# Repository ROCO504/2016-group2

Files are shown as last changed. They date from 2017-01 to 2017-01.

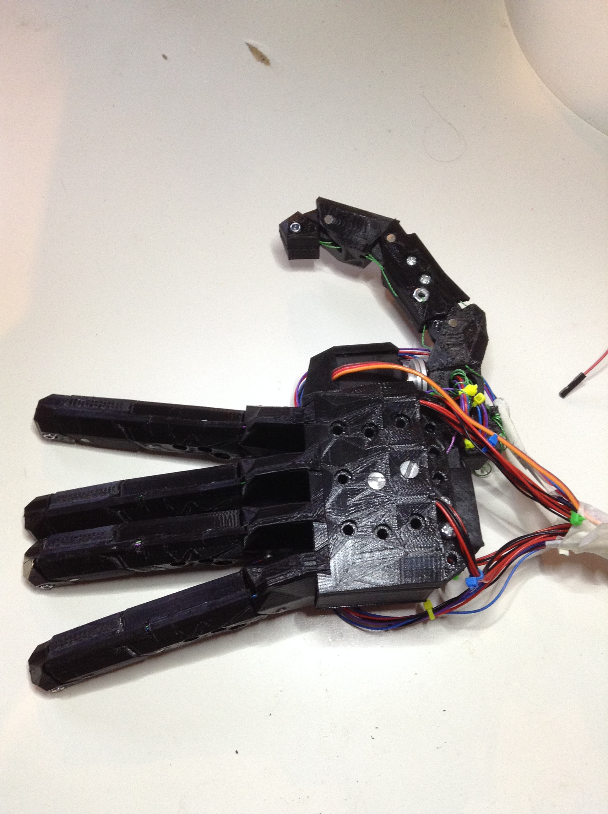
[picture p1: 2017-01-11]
presentaions/Pictures/IMG_2732.JPG

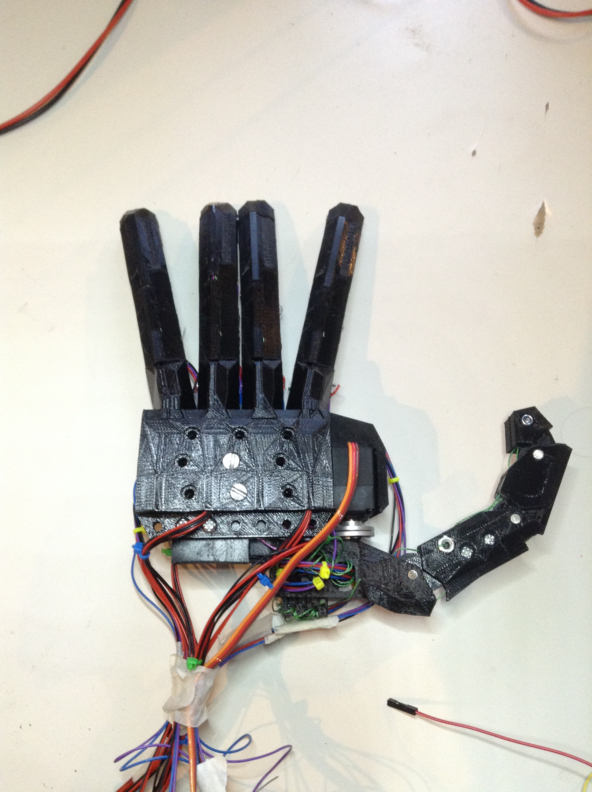
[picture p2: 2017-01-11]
presentaions/Pictures/IMG_2728.JPG

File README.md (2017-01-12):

# 2016-group2
Repository for the ROCO504 module at Plymouth University, UK.
Part of the MEng(Hons) Robotics programme in the School of Computing, Electronics and Mathematics.
The design files, code and picture been developed for the Soft Touch Robotic Hand Project.
The code has been designed for the Atmel ATtiny84 microcontroller using the 8MHz clock and for the Arduino Uno.
A video of the project in motion can be seen at the following youtube link:
https://www.youtube.com/watch?v=Z11QXyskEuM
The files are subject to the terms and conditions defined in the file 'LICENSE.md'.

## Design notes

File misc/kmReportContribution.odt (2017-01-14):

electrical

in order to implement the hand we had the following specifications:

- bi-directional speed control for 16 DC motors rated 12V 400mA
- position feedback for all drivable joints,with sufficient resolution to implement stable PID control.
- over-current and force-feedback for all motors.
- local controller capable of PID control and interpretation of inputs and feedback.
- common interface for control.
- Minimum size
- short turnaround

due to the short timescale ,there wasn't sufficient time to order a custom PCB, as such the entirety of the electronics needed to be designed to fit on single-sided dot-matrix prototyping boards. this limits the project to through-hole components on a 26 by 18, 0.1 inch grid.

In order to be able to read the current to each motor a pair of 1Ω 0.25W resisters in parallel are used as a high side shunt, for each motor driver. This gives a sense voltage of 12V to 11.8V.

This sense voltage is then be mapped to the 0-5V range of the intended microcontrollers ADC using a differential amplifier with a twenty five times gain.

A 5.1V zener is used to prevent damage to the ADC, should the motors draw over their rated current.

Cd4051 analogue multiplexers are used to cycle each sense line to the differential amplifier.

As these chips cannot be driven by TTL logic above an input voltage of ~10v each input requires a level shifter,in this case an NPN transistor.

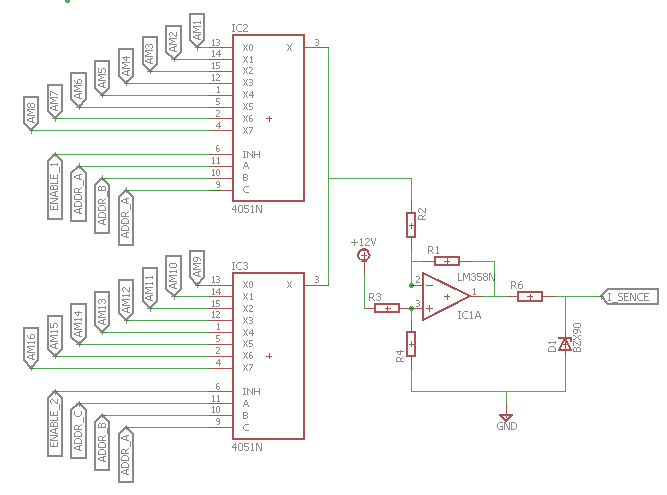
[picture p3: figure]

each motor requires a driver with separate power inputs ,in order to implement the current sensing ,and the projects limitation to through hole components ,this left the l9110 as the most practical chip.

note power should be distributed to the drivers in a star arrangement,such that all parasitic resistance from the cables is common to all drivers ,and thus eliminated by a correctly placed reference line,or unique to each, where errors can be removed in code.

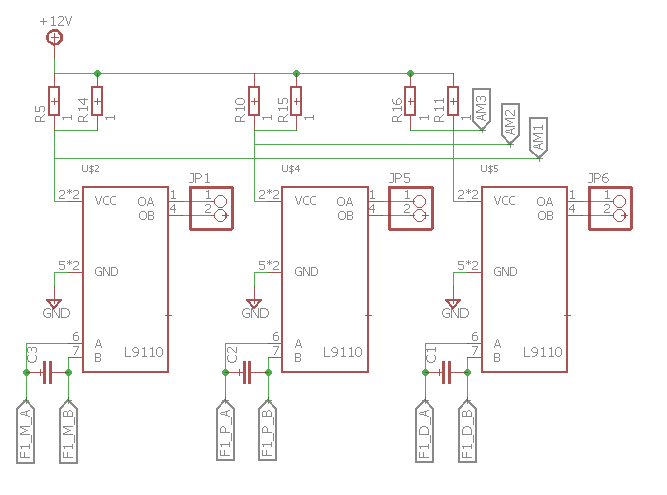
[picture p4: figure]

Position feedback is given using two potentiometers embedded in the driven joints. these are a generic trimmer potentiometer chosen for its low profile and square package. these can be powered from 5v and the output fed directly to the ADC.

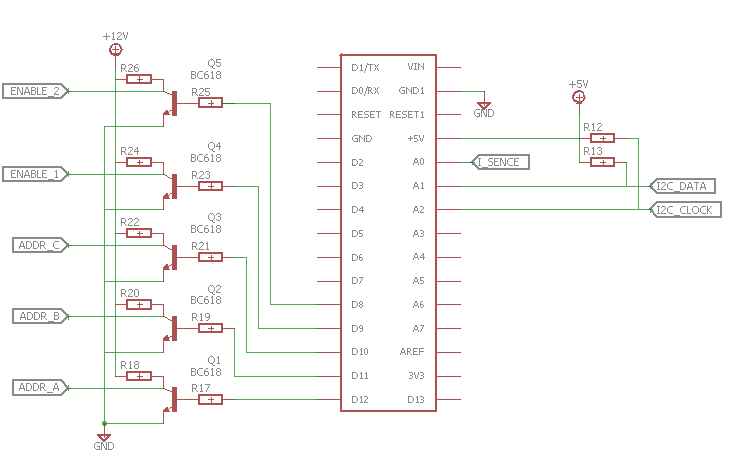
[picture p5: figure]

The thumb uses an analogue servo to rotate the finger around the wrist, as such it requires a DAC connection or a filtered pwm.

This gives 2 ADC connection and 6 GPIO connections per finger; with 5 GPIO and one ADC for the current sensing. and a DAC output for the servo.

As this is too much for a single through-hole microcontroller to interface with,the task was split, with an attiny84 controlling each finger And an Arduino nano sensing current as well as providing master control and a virtual serial port via USB. Communication between microcontrollers was implemented with a two wire interface.

  - 1.75mm 3d printing filament
  - less compliant than ninjaflex
- nylon scp
  - a 0.2mm solid nylon line,twisted until it formed a super coiled polymer
- double nylon scp
  - nylon scp twisted further to form a stable double helix
- pp scp
  - a multicore polypropylene twisted to form a super coiled polymer
  - soaked in a rubberising agent to stabilise.
- Pp
  - a polypropylene thread with a natural twist

discussion

as expected ,neither of the two tested Non-linear samples are suitable to the task. The elastic/nylon weave has a non-linear extension region of ~80% of the original length,considering its large diameter this would require an unfeasibly large spool to hold.

The ninjaflex/nylon has a more reasonable ~40% non-linear region,however there where issues in preventing the nylon from slipping,especially at high loads. considering the small volume available for mounting the material at each end,this isn't suitable.

The various SCPs showed plastic deformation at high loads, and are thus unstable for absorbing shocks.

The ninjaflex, semiflex and nylon all produced a nice linear force extension plots at various gradients, and will be our tendons,depending on the properties required. note, ninjaflex and semiflex is best held by melting the end and forming a head as knots slowly untie.

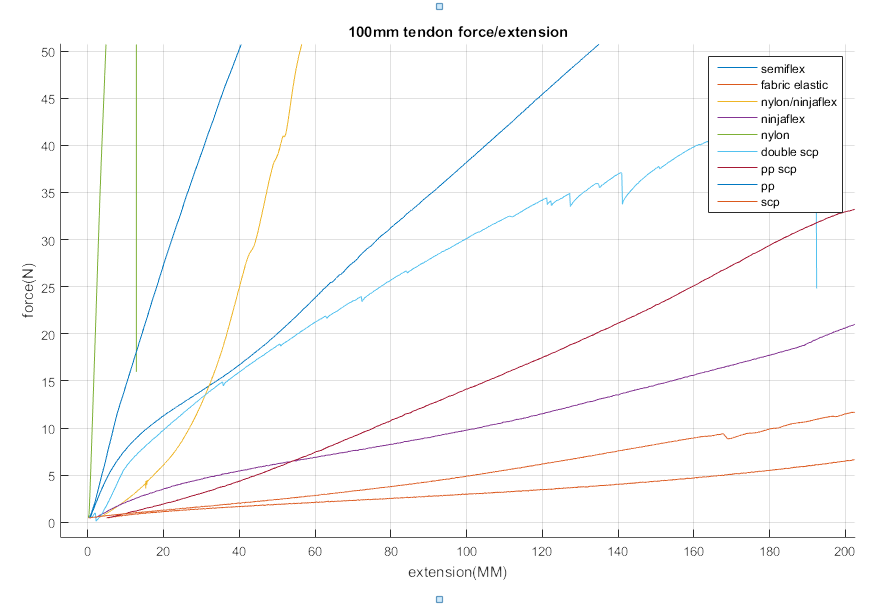
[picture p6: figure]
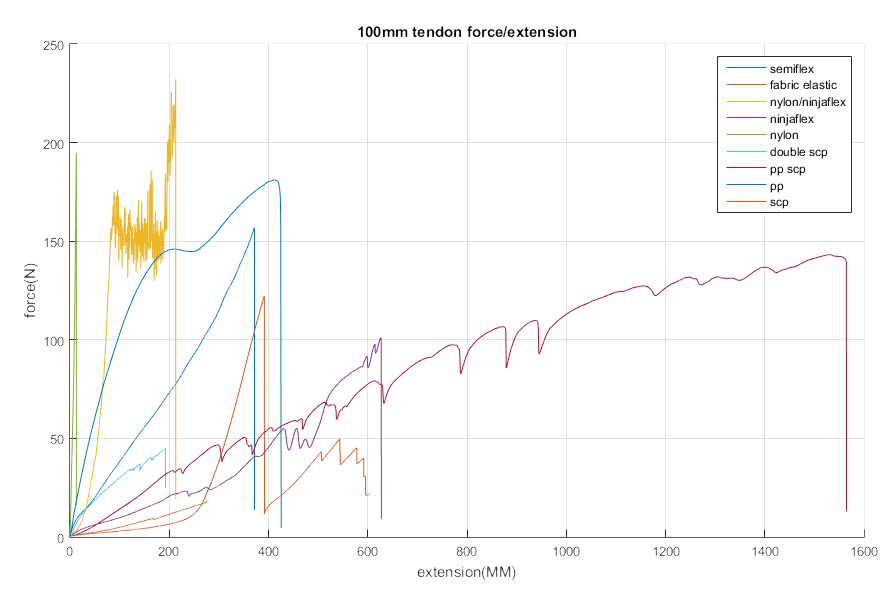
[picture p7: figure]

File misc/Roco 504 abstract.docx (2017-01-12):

Roco 504-abstract

Project: compliant humanoid hand

The intention is to produce a working humanoid hand that has variable stiffness actuation.

mechanical

Each finger is to have the metacarpal and proximal joints powered; the distal joint will be mechanically linked to move with the proximal joint.

The powered joints will be closed using geared dc motors, located in the palm, pulling sprung/elasticated tendons.

Extension for each finger will be passive by the use of a spring/elasticated tendon.

Variable stiffness will be achieved with the use of a motor applying tension to the return spring/tendon.

Positional feedback will be obtained from small potentiometers imbedded into the powered joints of each finger.

The thumb will have 3 powered joints and three potentiometers for feedback.

The fingers will be able to be spread using a mechanical linkage; A potentiometer will be used for feedback.

Electrical

To control the three bi-directional motors, and two potentiometers in each finger, a small microcontroller will be used (i.e. attiny 84), along with dedicated motor drivers.

A larger microcontroller will be used for the thumb as well as additional functions.

control will be in the form of pid positional regulation and feedback for each joint and communication with an external bus system (i.e. iic)

software

the intention is to link the hand to a computer running ROS, either by direct gpio or usb

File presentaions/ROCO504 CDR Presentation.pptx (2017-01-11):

## ROCO504 A Soft Touch CDR

Group 2: A-Team
Jake Shaw-Sutton, Isaac Chasteau, Khaian Marsh

## Introduction

- Design alterations
- Positional control
- Control Algorithm
- Variable compliance
- Limitations

## Design Alterations

## Pins

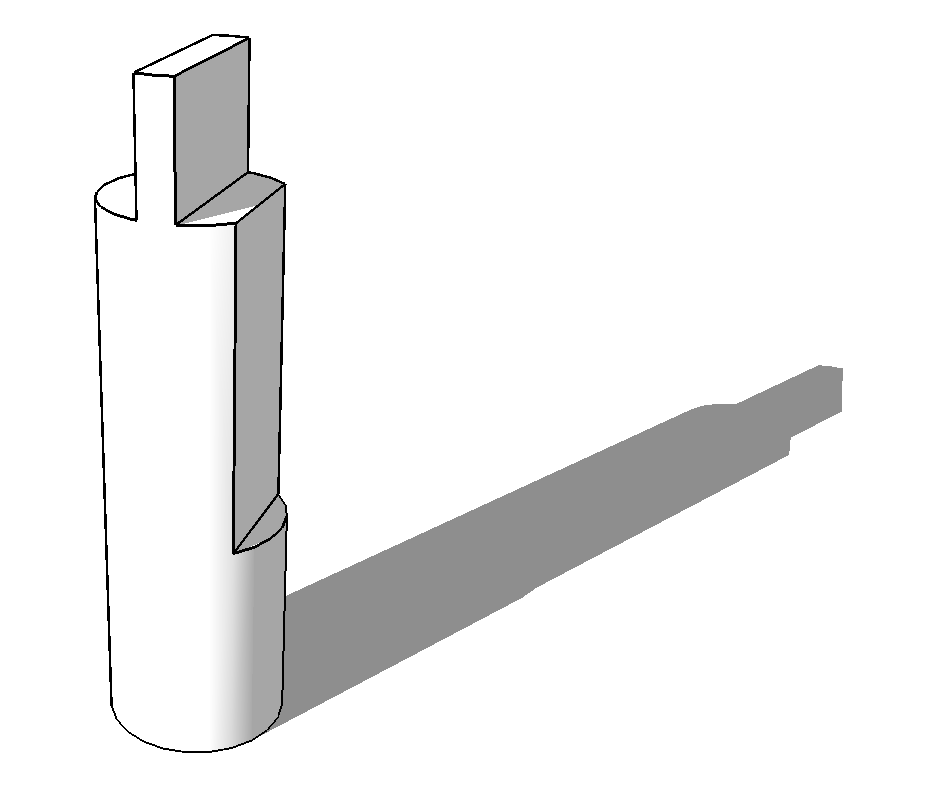
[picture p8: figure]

## Tendon Guide channels

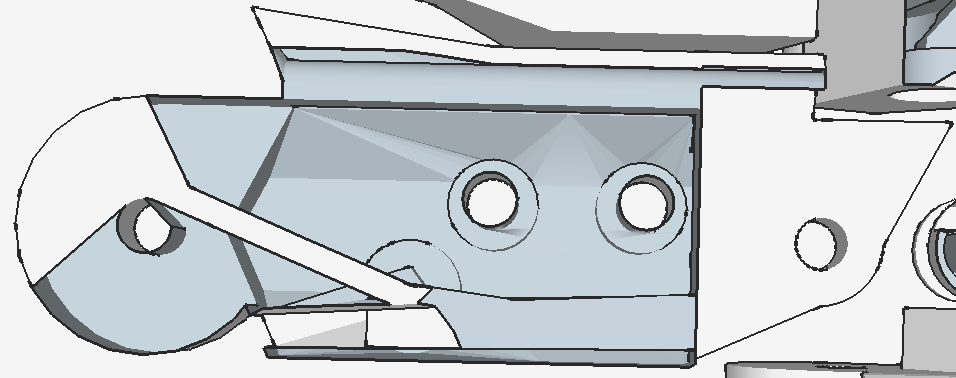
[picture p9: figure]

## Tendon composition

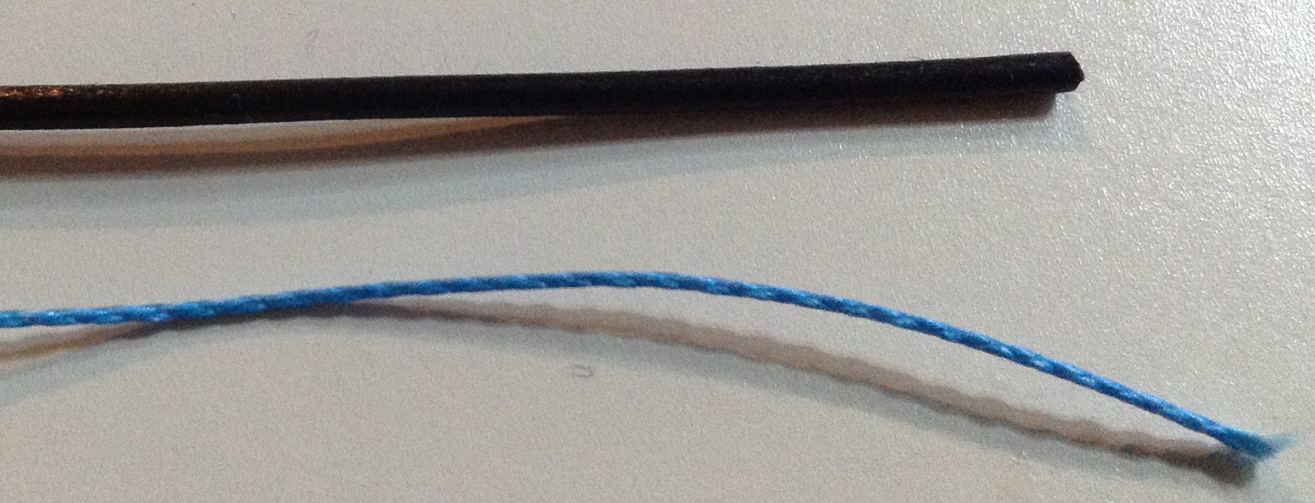
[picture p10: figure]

## Finger Joint proportions

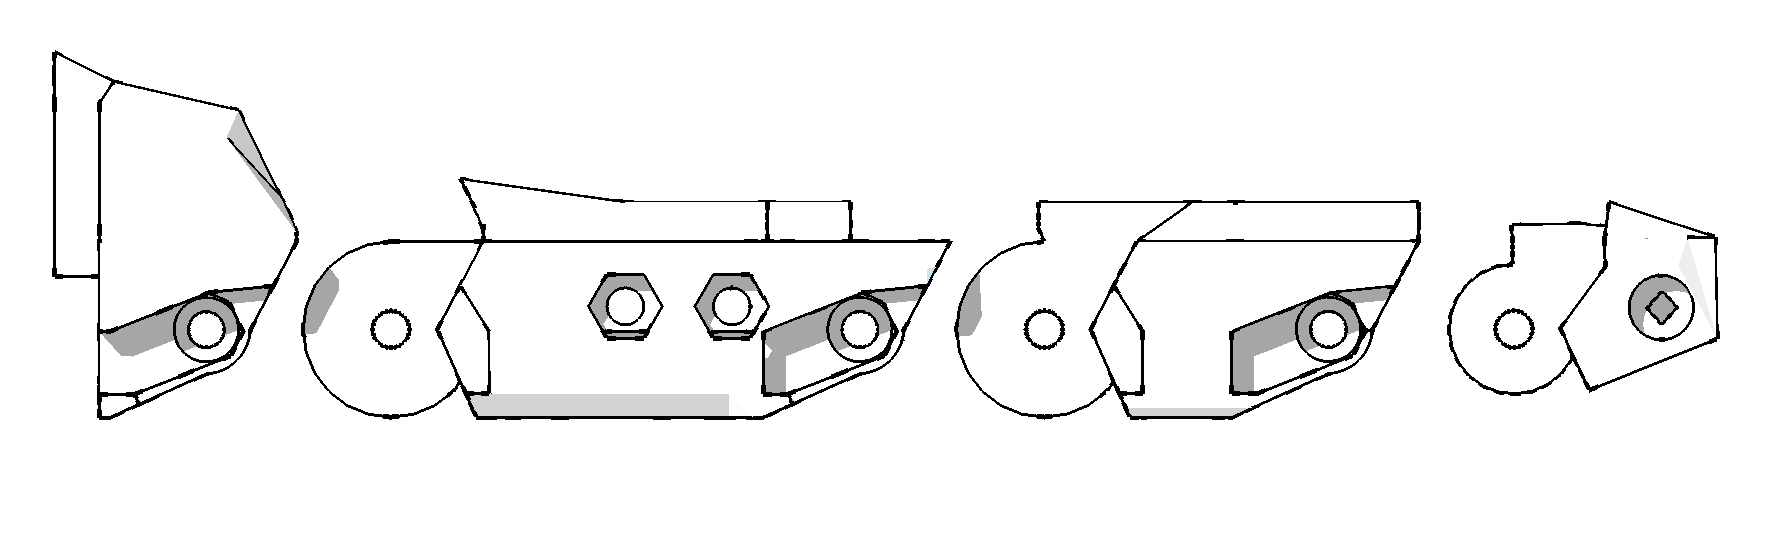
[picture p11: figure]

## Control Algorithm

- 2x Modified PID controllers
  - MCP and Proximal joint feedback
  - Decaying Integrals within target bounds
  - Proportionally scaled with respect to each others outputs
- 3 separate PWM cycles generated
- Proportional Pulsed Active Positioning

## Proportional Pulsed Active Positioning

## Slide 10

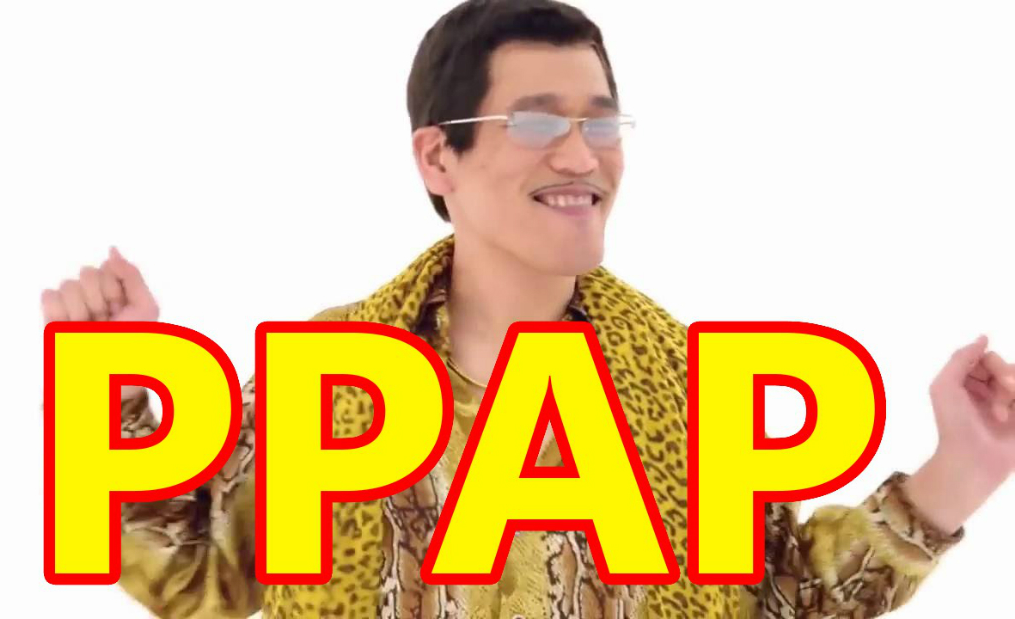
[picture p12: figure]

https://www.kpopvine.com/wp-content/uploads/PPAP.jpg

## MCP Positional correction

MCP and Distal Positional correction

Blue: MCP Orange: Proximal Red: Distal

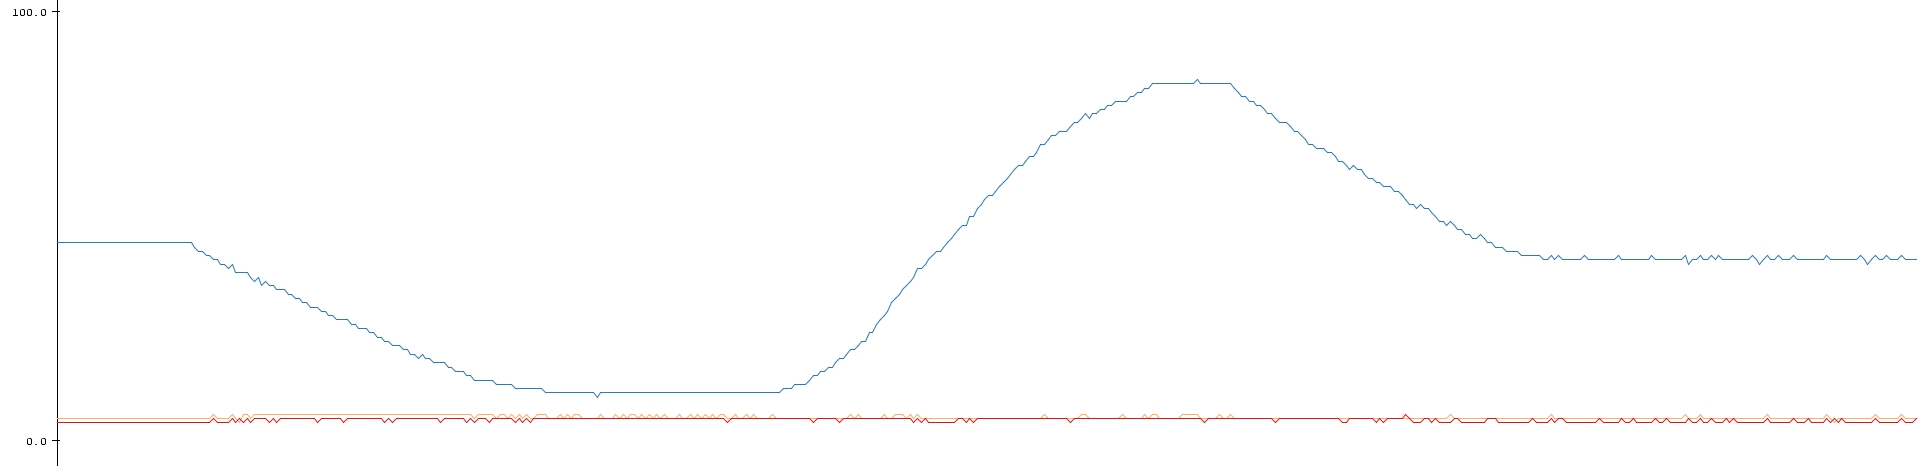
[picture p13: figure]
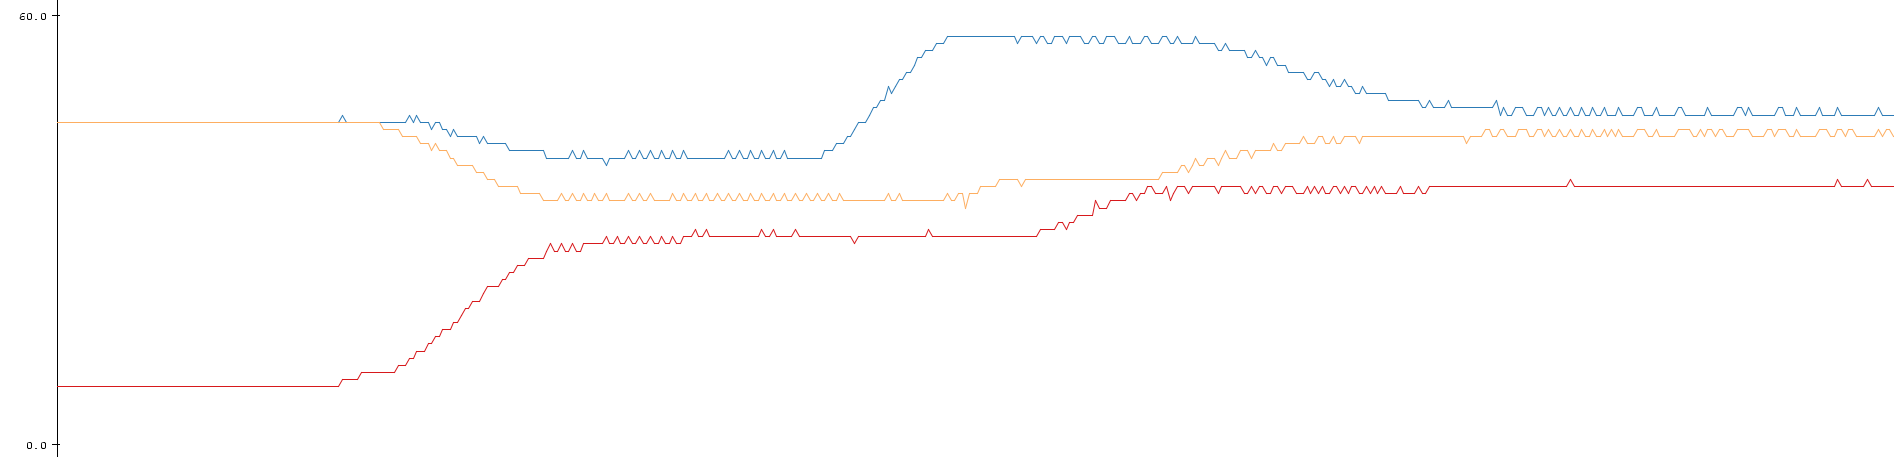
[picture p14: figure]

## Inverse Kinematics

ext=√(x^2 +y^2)
φ=cos^(−1) ((l_2^2 +l_1^2 −ext^2)/(2∙L_2 ∙L_1))
∆=cos^(−1) ((ext^2 +l_1^2 −l_2^2)/(2∙ext∙L_1))
δ=tan^(−1) (x/y)
θ=90−δ−∆
ω=180−φ
x_2 =sin(180−θ)∙L_3
y_2 =cos(180−θ)∙L_3
x=X_(target) −x_2
y=Y_(target) −y_2

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
## Variable Compliance

## Variable Compliance

- Variable compliance is achieved via co-contraction of the tendons

## Forced Impact Displacement with Co-contraction

## Limitations

- Touch feedback
- Motor Positional feedback
- Independent Distal Control
- Components

## Any Questions?

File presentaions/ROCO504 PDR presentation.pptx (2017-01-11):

## ROCO504 GROUP PROJECT

Advanced Robot Design

## Introduction to Project and Project Goals

## Introduction to Project and Project Goals

Title:

“A Soft Touch”

## Introduction to Project and Project Goals

Prosthetic Human Hand

## Introduction to Project and Project Goals

Prosthetic Human Hand
. Self Contained
. Variable Compliance
. Agonist-Antagonist Actuation

## Design Principle:

Actuated by 3 Motors :
-Palmar Joint
-Proximal and Distal Joint Linked
-Tension Tendon

Each Finger:

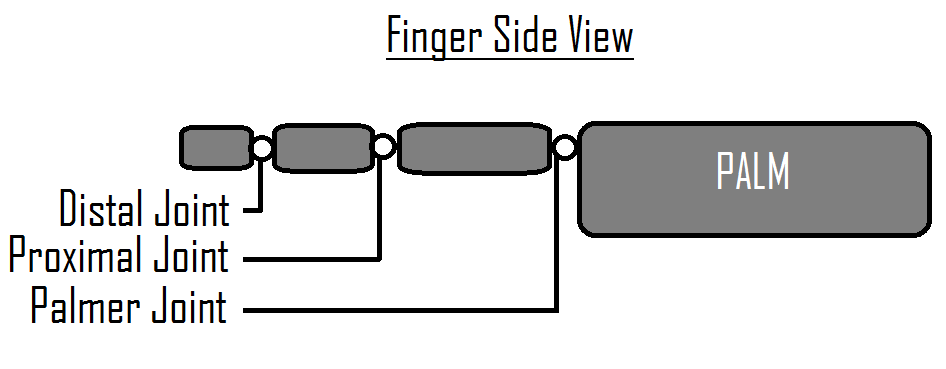
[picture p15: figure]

## Design Principle:

Made from a flexible material which is then winched

Materials:
Ninjaflex, Semiflex, PP, Nylon, Elastic

Tendons:

## Design Principle:

A Potentiometer Embedded in each Joint
Motor Current Reading

Feedback:

## Design:

CAD

## Design:

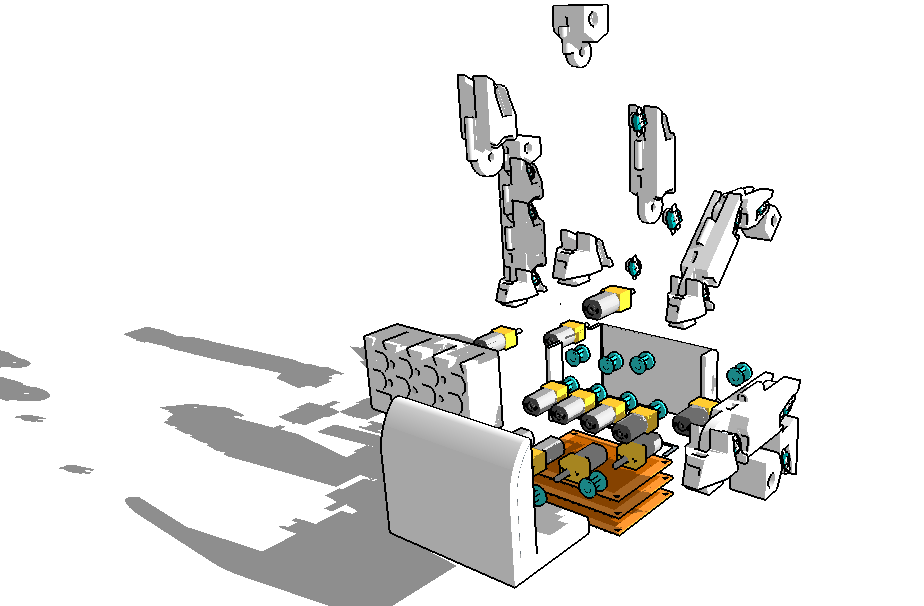
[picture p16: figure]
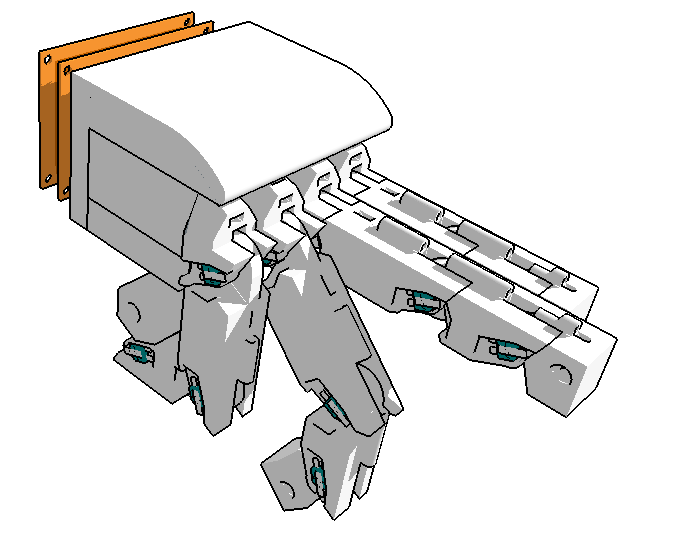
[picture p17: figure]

## Design:

Electronics

## Design:

Quantity | Component
16 | 12V 300RPM DC Motor with Gearbox
16 | L9110 Motor Drivers
16 | Shunt Resistors for current feedback
16 | Trim Potentiometers
5 | At-tiny 84
2 | 4051N 8-bit Analogue Shift Registers
1 | Arduino Nano
1 | LM358N Dual Op-Amp

## Design:

AT-Tiny 84 Pin-Out

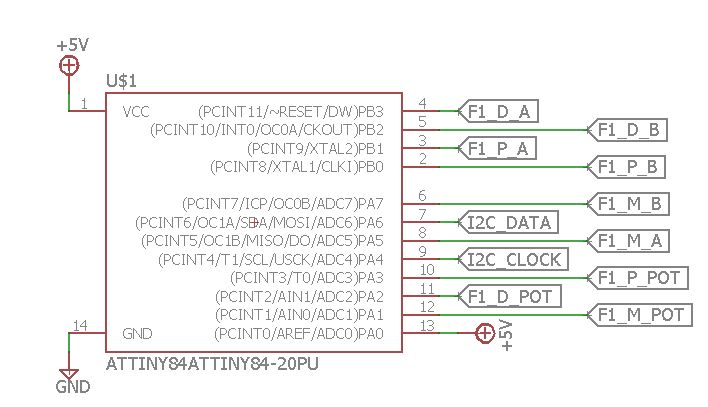
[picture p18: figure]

## Design:

Motor Driver Wiring Diagram

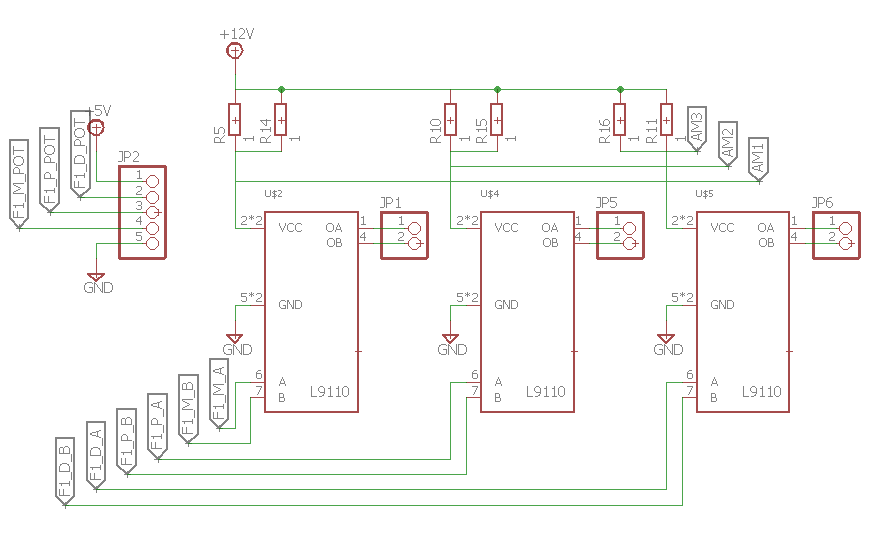
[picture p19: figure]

## Design:

Analogue Shift Register Wiring

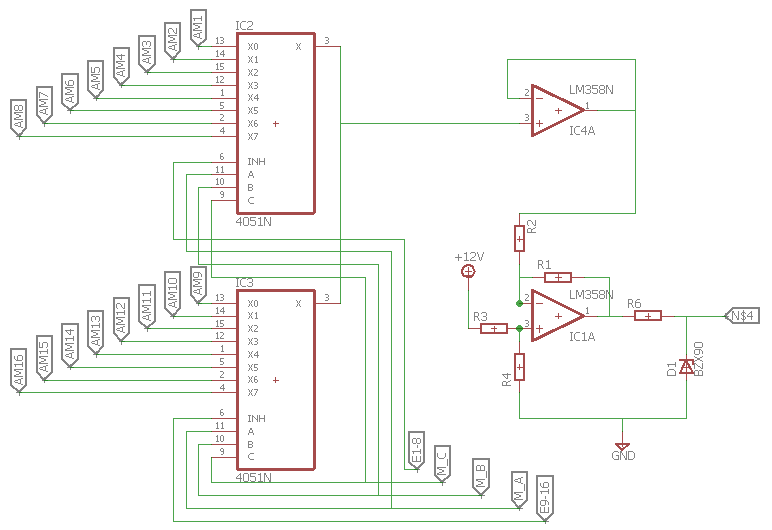
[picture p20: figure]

## Design: Compressed Wiring diagram for Circuit Board

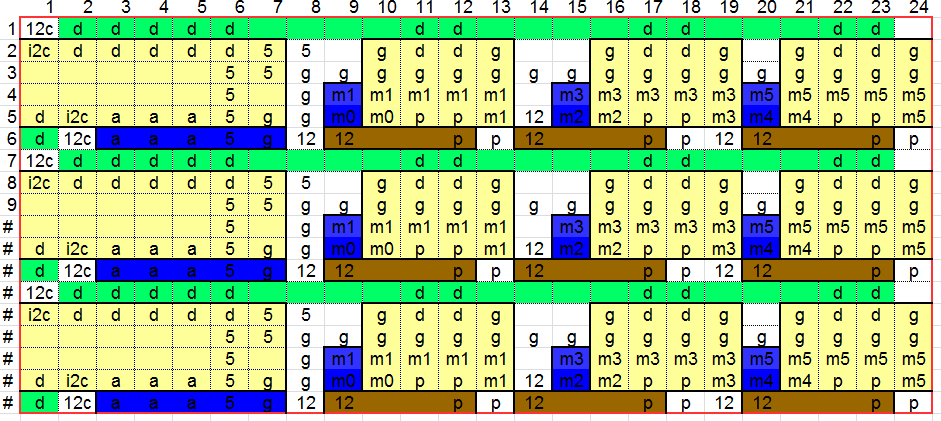
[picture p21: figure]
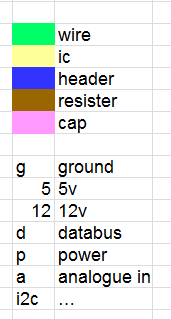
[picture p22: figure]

Proto-Matrix board templates, these act as wiring guides whilst manually soldering each of the 3 circuit boards.

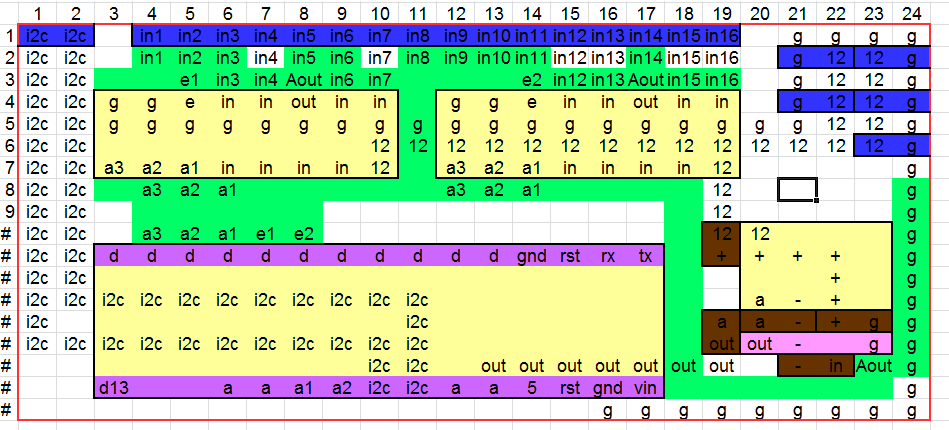
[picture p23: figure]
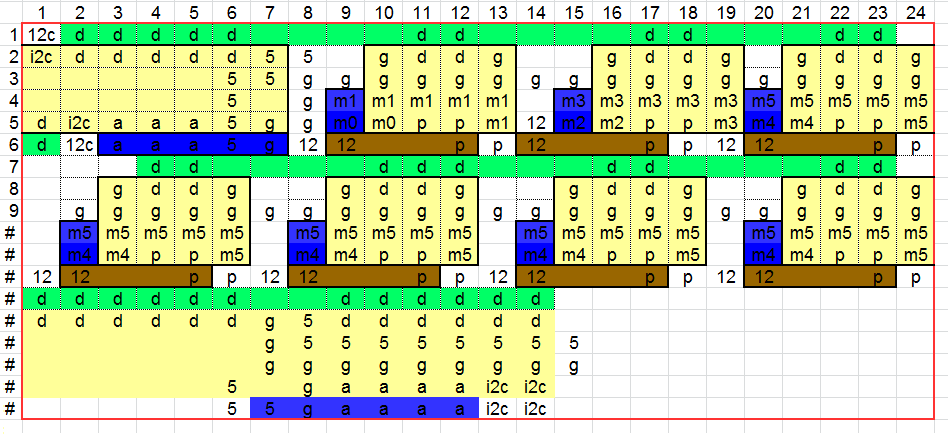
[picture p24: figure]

## Future Plan:

Gantt Chart

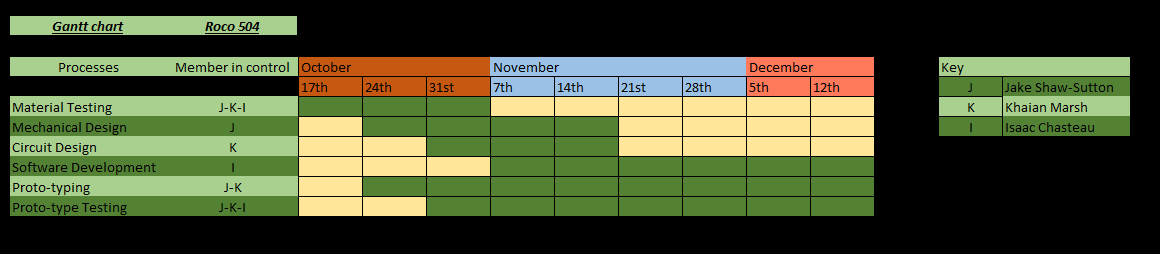
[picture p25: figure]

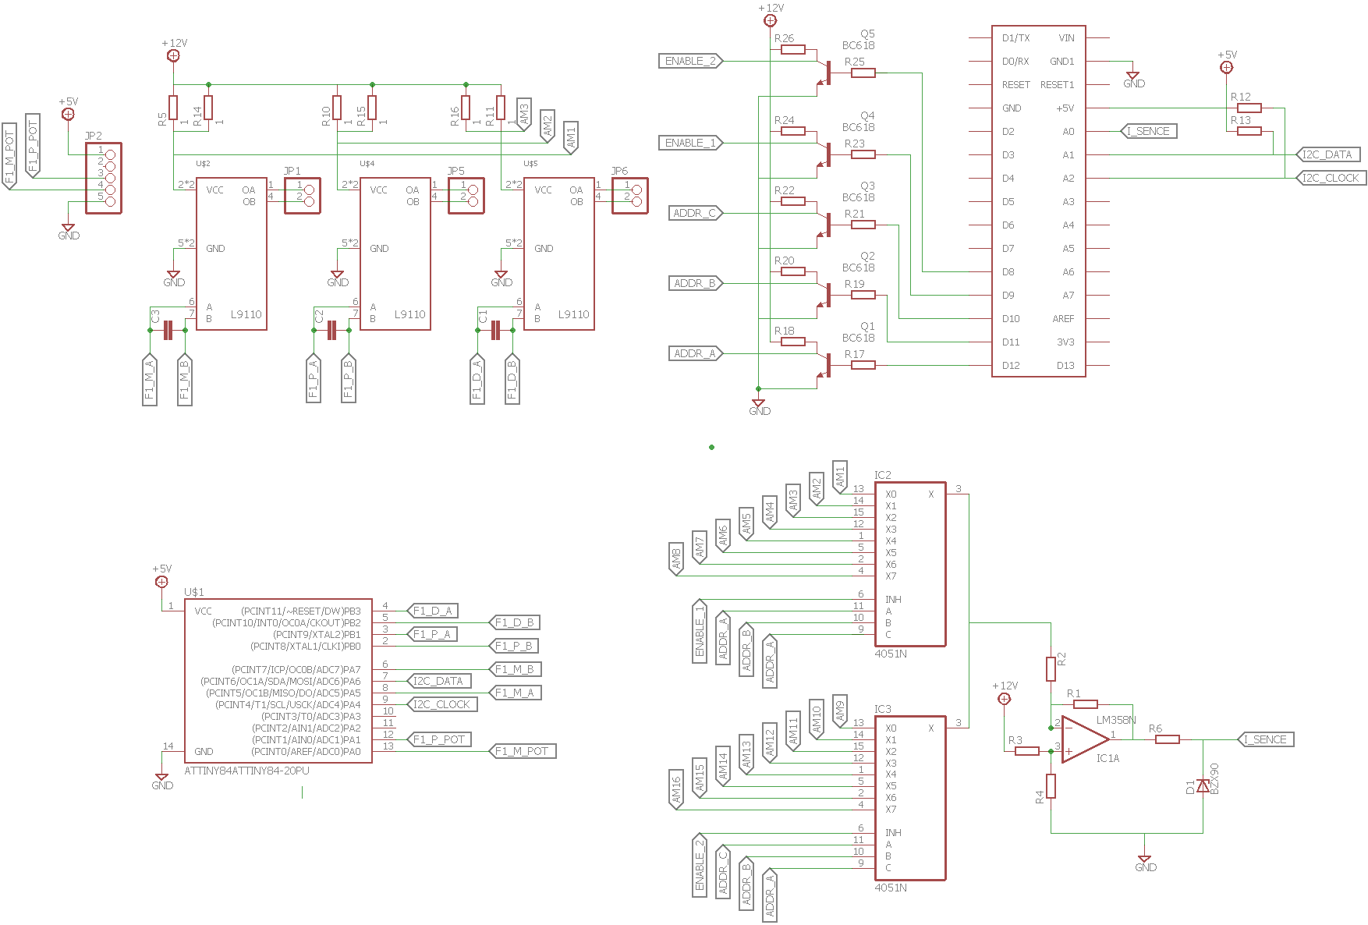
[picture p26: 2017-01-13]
circuit schematics/scematic.png

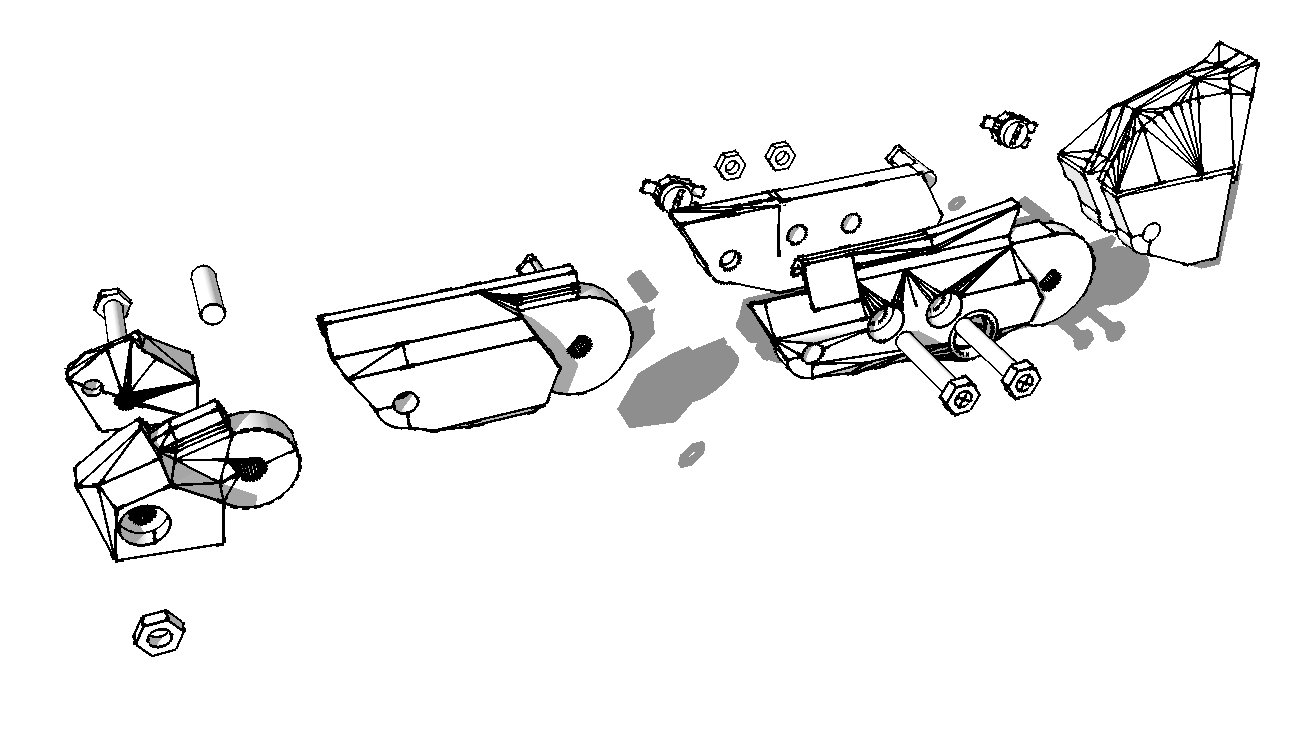
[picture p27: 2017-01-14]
CAD/Exploded finger 2.png

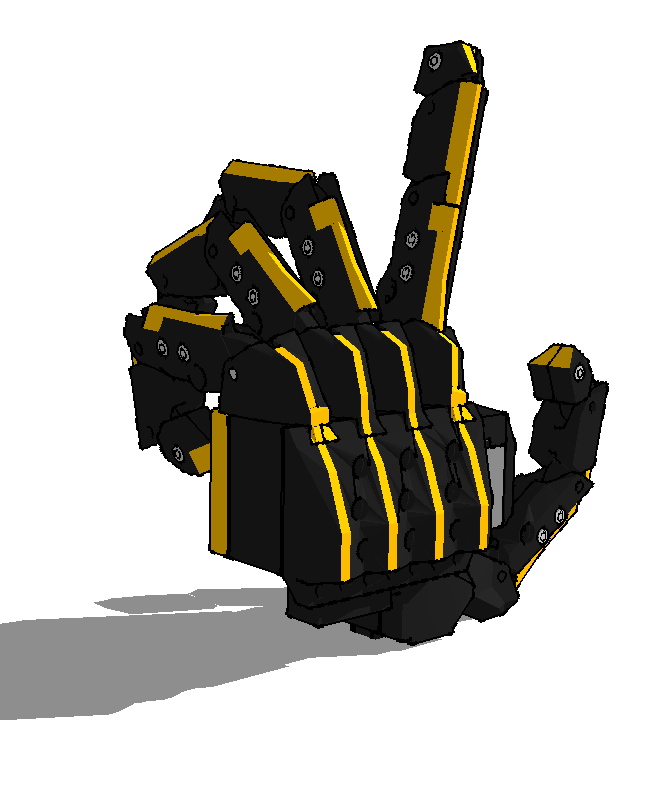
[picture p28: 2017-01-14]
CAD/Final hand 2.png

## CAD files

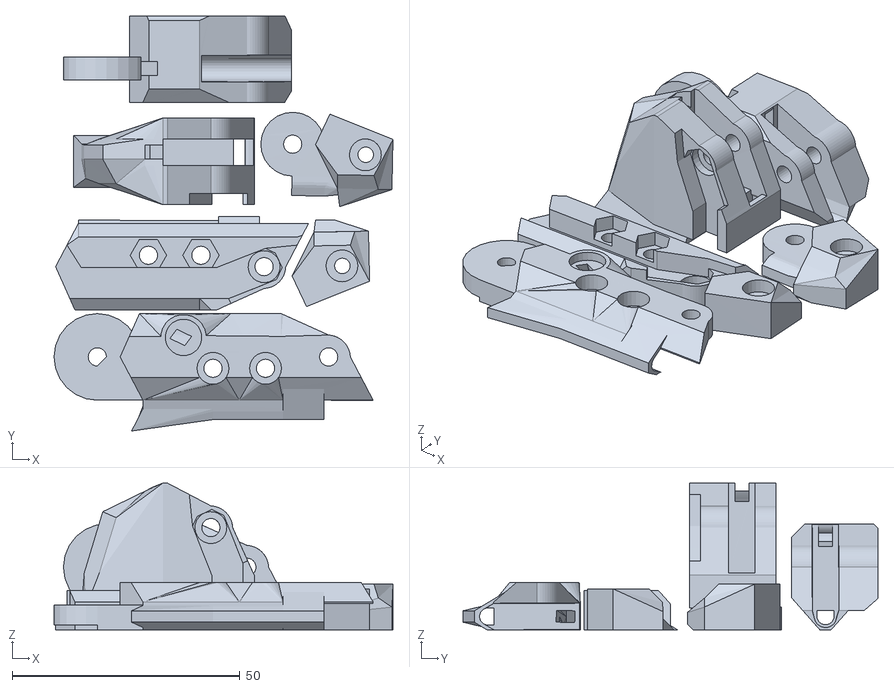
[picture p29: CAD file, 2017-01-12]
stl files/Complete Middle Finger.stl
74.3 x 91.0 x 32.2

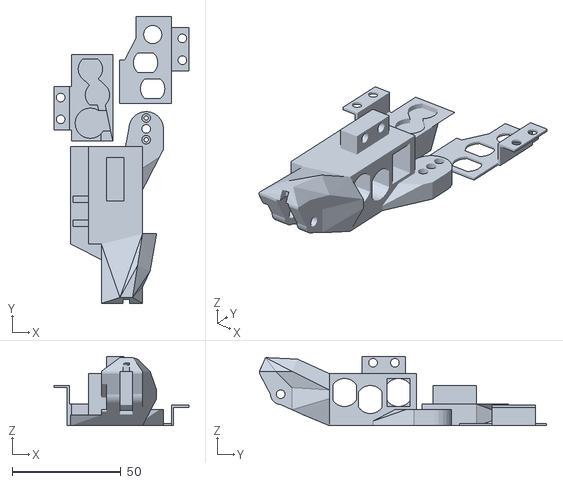
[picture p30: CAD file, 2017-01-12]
stl files/Thumb Knuckle.stl
62.0 x 132.2 x 32.0

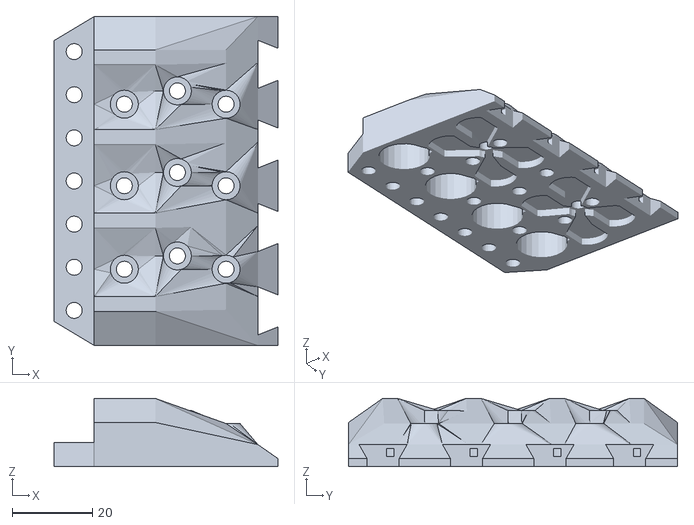
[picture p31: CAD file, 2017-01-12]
stl files/Hand Top Plate.stl
55.8 x 82.0 x 17.0

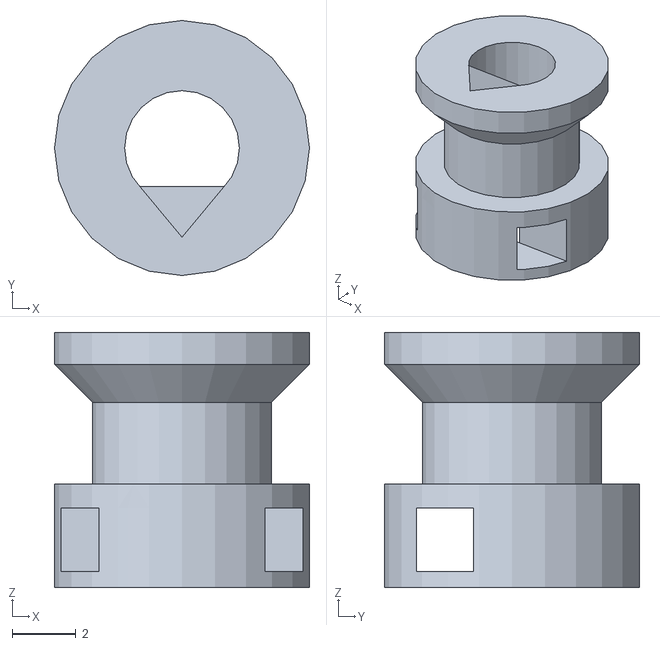
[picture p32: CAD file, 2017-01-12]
stl files/Pully.stl
8.00 x 8.00 x 8.00

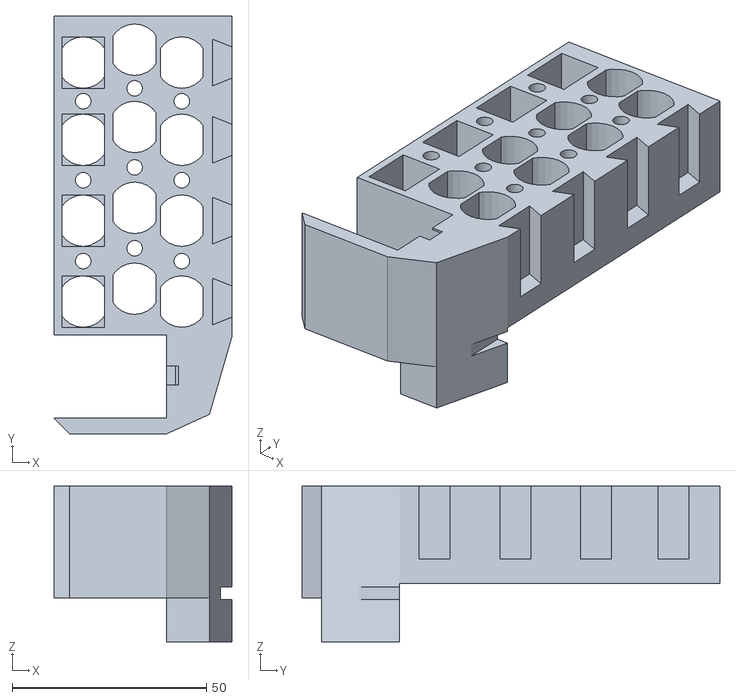
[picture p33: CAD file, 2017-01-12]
stl files/Palm Motor Block.stl
45.8 x 107.4 x 40.0

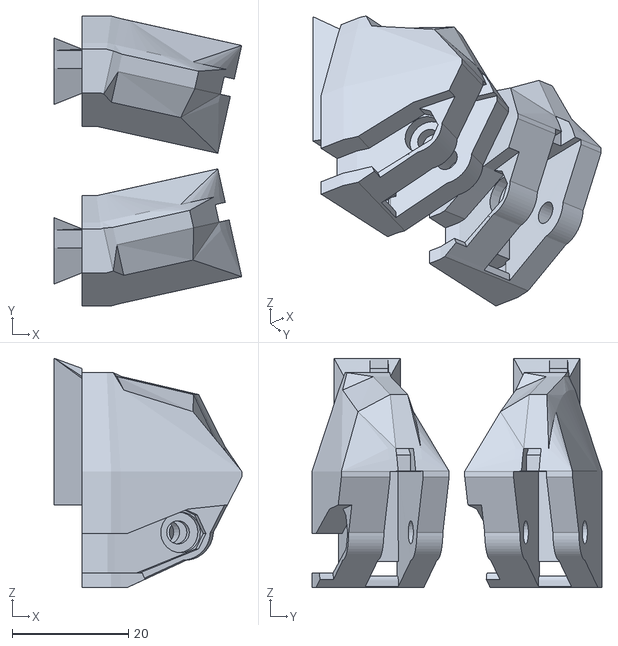
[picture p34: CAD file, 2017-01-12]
stl files/Angled Knuckles.stl
32.3 x 49.9 x 39.5

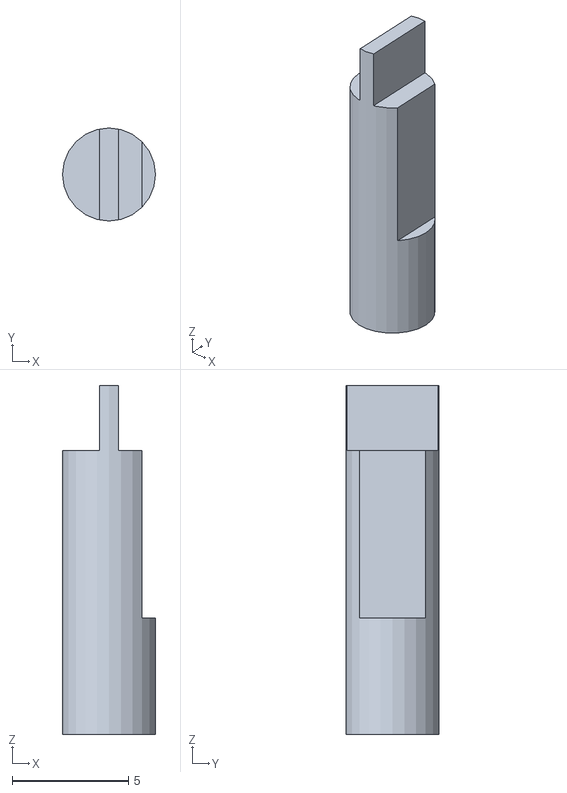
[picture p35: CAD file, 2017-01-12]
stl files/Pivot Pin.stl
4.00 x 4.00 x 15.0

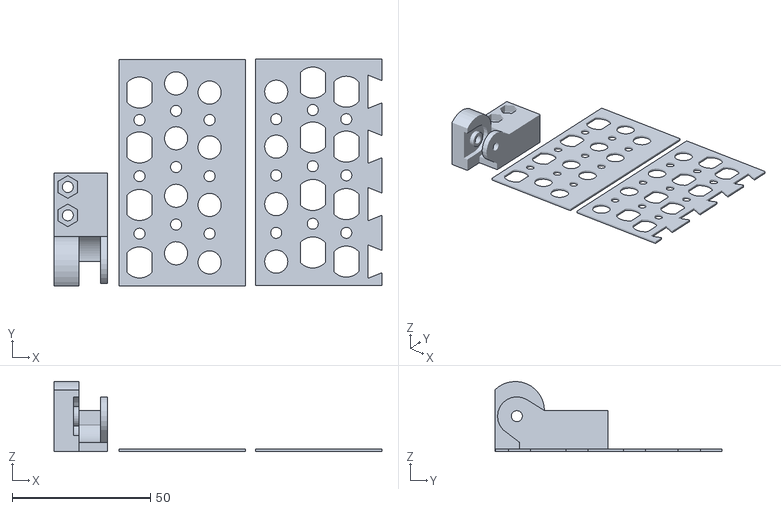
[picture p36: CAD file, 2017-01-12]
stl files/Thumb Bracket with Palm Plates.stl
118.7 x 82.3 x 25.4

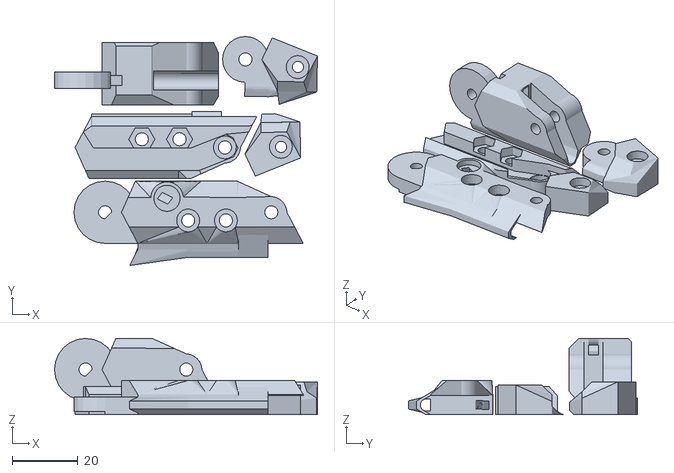
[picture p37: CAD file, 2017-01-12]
stl files/Finger Segments.stl
80.3 x 69.9 x 23.3

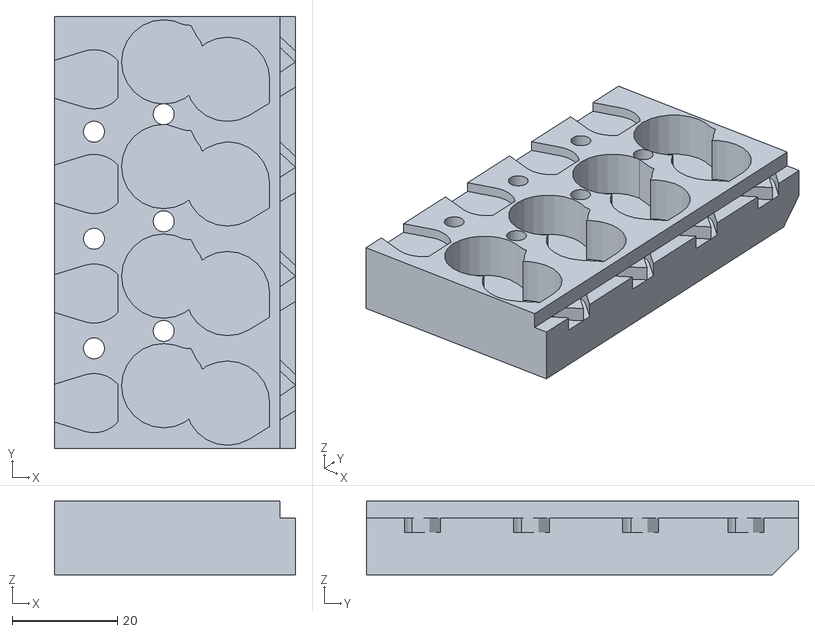
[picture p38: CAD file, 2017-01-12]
stl files/Palm Base Cover.stl
45.8 x 82.0 x 14.0

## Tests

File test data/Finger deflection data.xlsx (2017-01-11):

Method | MCP at 45 deg | Proximal at 5 deg | Deflection on Mt | 200g mass hung from the distal joint | Nylon tendons are used on Mt and Mp | Ninjaflex tendons are used on the MCP | Co-Contraction (%) | Current (A) | Method | MCP at 45 deg | Proximal at 5 deg | Deflection on Mm | 200g mass hung from the distal joint | Nylon tendons are used on Mt and Mp | Ninjaflex tendons are used on the MCP
 |  |  |  |  |  |  | Readings taken after all movement has stopped and the current ha settled
Co-contraction (%) | Mass (Kg) | Starting angle (deg) | Mass distance from MCP pivot (mm) | Mass distance from proximal pivot (mm) | MCP Deflection (deg) | Proximal Deflection (deg) | 0 | 0 | Co-contraction (%) | Mass (Kg) | Starting angle (deg) | Mass distance from MCP pivot (mm) | Mass distance from proximal pivot (mm) | MCP Deflection (deg) | Proximal Deflection (deg) |  | Lifting force (kg) | Lifting force (N) | Distance from pivot(mm)
0 | 0.2 | 45 | 86 | 36 | -36 | -26 | 10 | 0.16 | 0 | 0.1 | 45 | 86 | 36 | 26 |  | MCP | 0.063 | 0.61803 | 86
10 | 0.2 | 45 | 86 | 36 | 1 | 0 | 15 | 0.23 | 10 | 0.1 | 45 | 86 | 36 |  |  | Tension | 0.153 | 1.50093 | 86
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

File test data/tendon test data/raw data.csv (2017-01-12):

Extension | Load | Extension | Load | Extension | Load | Extension | Load | Extension | Load | Extension | Load | Extension | Load | Extension | Load | Extension | Load
(mm) | (N) | (mm) | (N) | (mm) | (N) | (mm) | (N) | (mm) | (N) | (mm) | (N) | (mm) | (N) | (mm) | (N) | (mm) | (N)
1.02 | 0.5 | 4.2 | 0.51 | 2.24 | 0.5 | 1.94 | 0.51 | 0.22 | 0.51 | 0.54 | 0.5 | 0.75 | 0.5 | 0.07 | 0.51 | 0.16 | 0.51
1.16 | 0.59 | 4.34 | 0.49 | 2.27 | 0.48 | 2.21 | 0.56 | 0.25 | 0.63 | 0.63 | 0.58 | 0.84 | 0.53 | 0.16 | 1.09 | 0.25 | 0.49
1.33 | 0.7 | 4.52 | 0.51 | 2.3 | 0.53 | 2.57 | 0.65 | 0.29 | 0.57 | 0.74 | 0.65 | 0.94 | 0.59 | 0.27 | 1.98 | 0.35 | 0.46
1.51 | 0.82 | 4.69 | 0.47 | 2.34 | 0.52 | 2.92 | 0.77 | 0.32 | 0.64 | 0.84 | 0.75 | 1.05 | 0.67 | 0.37 | 3 | 0.46 | 0.48
1.68 | 0.95 | 4.86 | 0.53 | 2.37 | 0.52 | 3.26 | 0.83 | 0.35 | 0.8 | 0.94 | 0.87 | 1.15 | 0.72 | 0.47 | 4.06 | 0.56 | 0.48
1.85 | 1.05 | 5.03 | 0.56 | 2.4 | 0.52 | 3.6 | 0.92 | 0.39 | 0.75 | 1.04 | 0.97 | 1.25 | 0.8 | 0.57 | 5.14 | 0.66 | 0.5
2.01 | 1.19 | 5.2 | 0.54 | 2.44 | 0.52 | 3.93 | 0.99 | 0.42 | 0.82 | 1.14 | 0.99 | 1.35 | 0.91 | 0.68 | 6.24 | 0.76 | 0.51
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

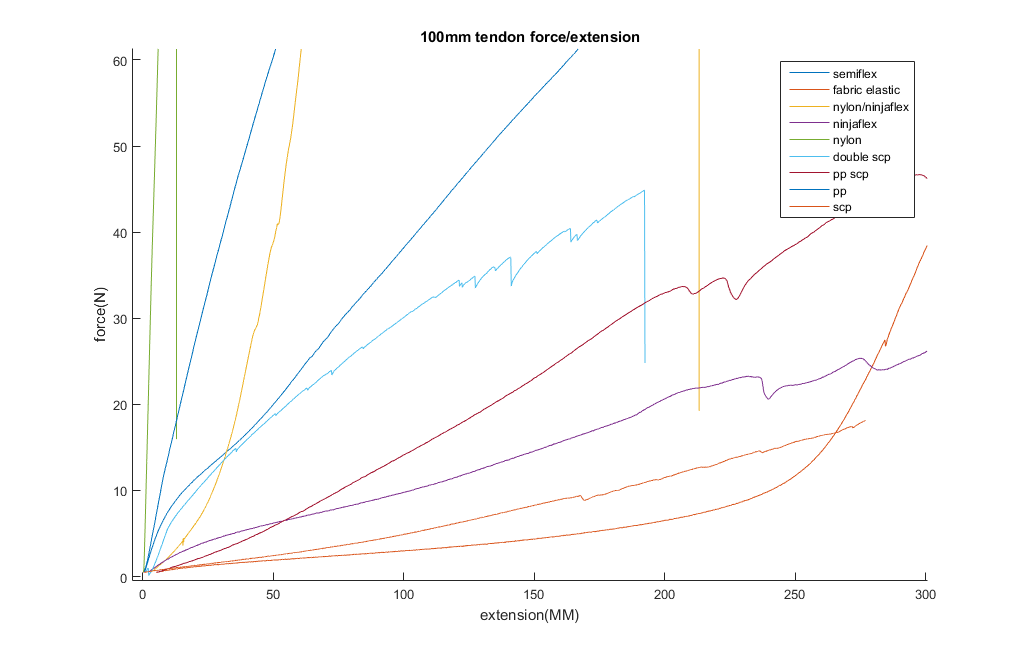
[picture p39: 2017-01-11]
test data/tendon test data/untitled2.bmp

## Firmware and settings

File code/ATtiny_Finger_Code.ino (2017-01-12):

/*--------------------------------------------------------------------------------------------------------------------
 * The code been developed for the Soft Touch Prosthetic Hand Project as part of the MEng Robotics ROCO504 Module at Plymouth University.
 * This code has been designed for the Atmel ATtiny84 microcontroller running at 8MHz.
 * This file is subject to the terms and conditions defined in the file 'LICENSE.txt'.
 * Written by Isaac Chasteau
 --------------------------------------------------------------------------------------------------------------------*/

#include <TinyWireS.h>
#include <ctype.h>

#ifndef TWI_RX_BUFFER_SIZE
#define TWI_RX_BUFFER_SIZE ( 16 )
#endif

/*--------------------------------------------------------------------------------------------------------------------
 * ATtiny84 I2C addresses
 * Index finger 0x4
 * Middle finger 0x5
 * Ring finger 0x6
 * Pinky finger 0x7
 * Thumb 0x8
 --------------------------------------------------------------------------------------------------------------------*/
 
#define I2C_SLAVE_ADDRESS 0x4// the 7-bit address (remember to change this when adapting this example)

//Defining the H-Bridge pins
#define IA_MCP PB2
#define IB_MCP PB0
#define IA_Proximal PA3//physical pin 6 (PWM)
#define IB_Proximal PB1
#define IA_Tension PA5//Physical pin 8
#define IB_Tension PA3//Physical pin 10(Digital)

//Defining the potentiometer pins
#define Proximal_pin PA2
#define MCP_pin PA1

//Defining PPAP parameters
#define Kp 18
#define Ki 0.45
#define Kd 500//My K/D you scrub

#define Kp1 25
#define Ki1 0.55
#define Kd1 600

#define integralUB 50
#define integralLB -50

#define minPWMpos 25
#define minPWMneg -30

#define minPWMpos1 35
#define minPWMneg1 -40

#define minMCPAngle 0
#define maxMCPAngle 90

#define minProximalAngle 0
#define maxProximalAngle 90

#define minCC 0
#define maxCC 102

int proximal_angle = 0;
int MCP_angle = 0;

//int previousTime = 0;
double previous_error = 0;
double integral = 0;
double derivative = 0;
double dt = 10;

//int previousTime1 = 0;
double previous_error1 = 0;
double integral1 = 0;
double derivative1 = 0;
double dt1 = 10;

int MCP_setPoint = 45;
int proximal_setPoint = 45;
int co_contraction = 0;

bool PID_cc_flag = false;
bool grip_flag = false;
bool PID_flag = true;
/*-------------------------------------------------------------------------------------------------------------------------------------------------*/

volatile uint8_t jointFeedback[] =
{
    0x0, 
    0x0, 
};

volatile uint8_t fingerVariables[] = //Holds the MCP and Proximal 
{
    0x1F, //MCP angle
    0x1F, //Proximal angle
    0x00, //Co-Contraction
};

volatile uint8_t bufferArray[] = //buffer 
{
    0x1F, //MCP angle
    0x1F, //Proximal angle
    0x00, //Co-Contraction
};
//const byte reg_size = sizeof(i2c_regs);
const byte fingerVariables_reg_size = sizeof(fingerVariables);
const byte two_reg_position_reg_size = sizeof(jointFeedback);
volatile byte reg_position = 0;
volatile byte three_reg_position = 0;
volatile byte two_reg_position = 0;
volatile byte reg_pos = 0;

/*-------------------------------------------------------------------------------------------------------------------------------------------------*/

void updateJointValues(void){
  proximal_angle = analogRead(Proximal_pin);//readADC(2);//analogRead(Proximal_pin);
  MCP_angle = analogRead(MCP_pin);//readADC(1);//analogRead(MCP_pin);
  if(I2C_SLAVE_ADDRESS == 0x4){//Index finger
    proximal_angle = map(proximal_angle, 400, 860, 0, 90);
    MCP_angle = map(MCP_angle, 550, 840, 0, 90);
  }else if(I2C_SLAVE_ADDRESS == 0x5){//Middle finger
    proximal_angle = map(proximal_angle, 516, 988, 0, 90);
    MCP_angle = map(MCP_angle, 576, 1020, 0, 90);
  }else if(I2C_SLAVE_ADDRESS == 0x6){//Ring finger
    proximal_angle = map(proximal_angle, 590, 1020, 0, 90);
    MCP_angle = map(MCP_angle, 340, 804, 0, 90);
  }else if(I2C_SLAVE_ADDRESS == 0x7){//Pinky finger
    proximal_angle = map(proximal_angle, 330, 744, 0, 90);
    MCP_angle = map(MCP_angle, 550, 950, 0, 90);
  }else if(I2C_SLAVE_ADDRESS == 0x8){//Thumb
    proximal_angle = map(proximal_angle, 390, 820, 0, 90);
    MCP_angle = map(MCP_angle, 410, 840, 0, 90);
  }
  jointFeedback[0] = MCP_angle;
  jointFeedback[1] = proximal_angle;
}

/*-------------------------------------------------------------------------------------------------------------------------------------------------*/

void requestEvent()
{  
  TinyWireS.send(jointFeedback[two_reg_position]);
  two_reg_position++;
  if (two_reg_position >= two_reg_position_reg_size)
  {
    two_reg_position = 0;
  }
}

/*-------------------------------------------------------------------------------------------------------------------------------------------------*/

void receiveEvent(uint8_t howMany)
{
  if (howMany < 1)return;// Sanity-check
  if (howMany > TWI_RX_BUFFER_SIZE) return;
  if (!howMany) return; // This write was only to set the buffer for next read
  if (howMany != 3)return;//if it doesn't receive 3 bytes
  while(howMany--)
  {
    bufferArray[reg_pos] = TinyWireS.receive();//read in the data and stores it.
    if(bufferArray[reg_pos] == 101){ 
      bufferArray[reg_pos] = 0;
    }
    reg_pos++;
    if (reg_pos >= fingerVariables_reg_size)
    {
      reg_pos = 0;
      break;
    }
  }
  //Verifies the data is in the correct ranges
  if(bufferArray[0] < minMCPAngle || bufferArray[0] > maxMCPAngle )return;
  if(bufferArray[1] < minProximalAngle || bufferArray[1] > maxProximalAngle )return;
  if(bufferArray[2] < minCC || bufferArray[2] > maxCC )return;
  
  for(int i = 0; i < fingerVariables_reg_size; i++){//Sets the fingerVariable array to the bufferArray values
    fingerVariables[i] = bufferArray[i];
  }
  update_setpoints();
}

/*-------------------------------------------------------------------------------------------------------------------------------------------------*/

void update_setpoints(void){
  MCP_setPoint = fingerVariables[0];
  proximal_setPoint = fingerVariables[1];
  co_contraction = fingerVariables[2];

  if(co_contraction == 0){
    PID_flag = true;
    PID_cc_flag = false;
    grip_flag = false;
  }else if(co_contraction > 0 && co_contraction <= 100){
    PID_flag = false;
    PID_cc_flag = true;
    grip_flag = false;
  }else if(co_contraction == 102){
    PID_flag = false;
    PID_cc_flag = true;
    grip_flag = true;
  }
}

/*-------------------------------------------------------------------------------------------------------------------------------------------------*/

void motorDriver(int pwm, int motorNum){
  if(motorNum == 0){
    if (pwm >= 0){//If PWM is positive
      analogWrite(IA_MCP, pwm);
      PORTB &= (~(1<<IB_MCP));
    }else if(pwm < 0){//If PWM in negative 
      PORTB |= (1<<IB_MCP);//IB is set high
      analogWrite(IA_MCP, 255+pwm);//IA is a PWM of 255 minus the negative PWM
    }
  }else if(motorNum == 1){
    if (pwm >= 0){//If PWM is positive
      analogWrite(IA_Proximal, pwm);
      PORTB &= (~(1<<IB_Proximal));
    }else if(pwm < 0){//If PWM in negative 
      PORTB |= (1<<IB_Proximal);//IB is set high
      analogWrite(IA_Proximal, 255+pwm);//IA is a PWM of 255 minus the negative PWM
    }
  }else if(motorNum == 2){
    if (pwm >= 0){//If PWM is positive
      analogWrite(IA_Tension, pwm);
      PORTA &= (~(1<<IB_Tension));
    }else if(pwm < 0){//If PWM in negative 
      PORTA |= (1<<IB_Tension);//IB is set high
      analogWrite(IA_Tension, 255+pwm);//IA is a PWM of 255 minus the negative PWM
    }
  }
}

/*-------------------------------------------------------------------------------------------------------------------------------------------------*/

int MmPID(int error){//MCP joint PID
  //dt = millis() - previousTime;//time elapsed
  if(abs(error) < 2)error = 0;
  integral += error * dt;
  if(integral > integralUB){//Sets integral limits to prevent integral windup
    integral = integralUB;
  }else if(integral < integralLB){
    integral = integralLB;
  }else if(error < 4 && error > -4){
    integral *= 0.3;//0.2
  }
  
  derivative = (error - previous_error)/dt;
  double output = Kp*error + Ki*integral + Kd*derivative;
  previous_error = error;
 
  if(output > 255){
    output = 255;
  }else if(output < -255){
    output = -255;
  }else if(output > 2 && output < minPWMpos){
    output = minPWMpos;
  }else if(output < -2 && output > minPWMneg){
    output = minPWMneg;
  }
  
  int PWMout = round(output);
  return PWMout;//Returns the PID output
}

/*-------------------------------------------------------------------------------------------------------------------------------------------------*/

int MpPID(int error){//Proximal joint PID
  if(abs(error) < 2)error = 0;
  integral1 += error * dt1;
  if(integral1 > integralUB){//Sets integral limits to prevent integral windup
    integral1 = integralUB;
  }else if(integral1 < integralLB){
    integral1 = integralLB;
  }else if(error < 4 && error > -4){
    integral1 *= 0.3;
  }
  
  derivative1 = (error - previous_error1)/dt1;
  double output = Kp1*error + Ki1*integral1 + Kd1*derivative1;
  previous_error1 = error;
  
  if(output > 255){
    output = 255;
  }else if(output < -255){
    output = -255;
  }else if(output > 2 && output < minPWMpos1){
    output = minPWMpos1;
  }else if(output < -2 && output > minPWMneg1){
    output = minPWMneg1;
  }
  
  int PWMout = round(output);
  return PWMout;//Returns the PID output
}

/*-------------------------------------------------------------------------------------------------------------------------------------------------*/

void setFingerPos(int MmTheta, int MpTheta){
  if(MmTheta < 0 || MmTheta > 90 ||  MpTheta < 0 ||  MpTheta > 90)return;
  updateJointValues();
  int Mm_error = MmTheta - ::MCP_angle;
  int Mp_error = MpTheta - ::proximal_angle;
  
  int Mm_PWM = MmPID(Mm_error);
  int Mp_PWM = MpPID(Mp_error);

  //limits the PWMs to match the Maximum the tension line can operate
  if(abs(Mm_PWM + Mp_PWM) > 255){
    Mm_PWM *= ((double)Mm_PWM / ((double)Mm_PWM + (double)Mp_PWM));
    Mp_PWM *= ((double)Mm_PWM / ((double)Mm_PWM + (double)Mp_PWM));
  }
  fingerMotorControl(Mm_PWM, Mp_PWM);
}

/*-------------------------------------------------------------------------------------------------------------------------------------------------*/

void fingerMotorControl(int Mm_PWM, int Mp_PWM){
  int Mt_PWM = Mm_PWM + Mp_PWM;
  if(abs(Mt_PWM) > 255){
    return;//check the values are in range
  }
  if(Mt_PWM > 0){
    Mt_PWM *= 0.7;
  }else if(Mt_PWM < 0){
    Mm_PWM *= 0.5;
    Mp_PWM *= 0.6;
  }
  motorDriver(Mt_PWM, 2);//Tension line
  motorDriver(Mp_PWM, 1);//Proximal line
  motorDriver(Mm_PWM, 0);//MCP line
}

/*-------------------------------------------------------------------------------------------------------------------------------------------------*/

void Co_Contraction(int percentageCC){
  if(percentageCC > 100) return;
  if(percentageCC < 10){
    motorDriver(0, 2);//Tension line
    motorDriver(0, 1);//Proximal line
    motorDriver(0, 0);//MCP line
    return;
  }
  
  int Mt_PWM = map(percentageCC, 10, 100, -20, -60);
  int Mp_PWM = map(percentageCC, 10, 100, 30, 255);
  int Mm_PWM = map(percentageCC, 0, 100, 0, 255);
  motorDriver(Mt_PWM, 2);//Tension line
  motorDriver(Mp_PWM, 1);//Proximal line
  motorDriver(Mm_PWM, 0);//MCP line
}

/*-------------------------------------------------------------------------------------------------------------------------------------------------*/

void grip(int loosen, int Mm_percentage, int Mp_percentage){
  if(Mm_percentage < 0 || Mm_percentage > 100 || Mp_percentage < 0 || Mp_percentage > 100)return;
  
  int Mp_PWM = map(Mp_percentage, 0, 100, 0, 255);
  int Mm_PWM = map(Mm_percentage, 0, 100, 0, 255);
  
  if(abs(Mm_PWM + Mp_PWM) > 255){//Scales the max pwms
    Mm_PWM *= ((double)Mm_PWM / ((double)Mm_PWM + (double)Mp_PWM));
    Mp_PWM *= ((double)Mm_PWM / ((double)Mm_PWM + (double)Mp_PWM));
  }
  int Mt_PWM = (Mm_PWM + Mp_PWM) * 0.7;
  motorDriver(Mt_PWM, 2);//Tension line
  motorDriver(Mp_PWM, 1);//Proximal line
  motorDriver(Mm_PWM, 0);//MCP line
  delay(loosen);
  motorDriver(0, 2);//Turn the tension line off
  grip_flag = false;
}

/*-------------------------------------------------------------------------------------------------------------------------------------------------*/

void co_contraction_PID(int co_contraction){
  if(!PID_cc_flag)return;
  unsigned long startTime = millis();//get current time
  while(millis() - startTime < 800  ){//loop for 800ms
    setFingerPos(MCP_setPoint, proximal_setPoint);//The PPAP control
  }
  Co_Contraction(co_contraction);//Sets the co_contraction
  PID_cc_flag = false;
}

/*-------------------------------------------------------------------------------------------------------------------------------------------------*/

void tighten_pulleys(int ms){
  motorDriver(-70, 2);//Tension line
  motorDriver(70, 1);//Proximal line
  motorDriver(70, 0);//MCP line
  delay(ms);
  motorDriver(0, 2);//Tension line
  motorDriver(0, 1);//Proximal line
  motorDriver(0, 0);//MCP line
}

/*-------------------------------------------------------------------------------------------------------------------------------------------------*/

void setup()
{
//Set up all pins to the correct mode
  pinMode(IA_MCP, OUTPUT);
  DDRB |= (1<<DDB0);//Sets the pins data direction register to write (output)
  pinMode(IA_Proximal, OUTPUT);
  DDRB |= (1<<DDB1);//Sets the pins data direction register to write (output)
  pinMode(IA_Tension, OUTPUT);
  DDRA |= (1<<DDA3);//Sets the pins data direction register to write (output)

  DDRA &= (~(1<<Proximal_pin));//Sets the pin to an input
  DDRA &= (~(1<<MCP_pin));//Sets the pin to an input

  DIDR0 |= (1<<ADC1D);//Disable digital register on the analog pin1
  DIDR0 |= (1<<ADC2D);//Disable digital register on the analog pin2
  
  //Ensure all pins are set low
  analogWrite(IA_MCP, 0);
  PORTB &= (~(1<<IB_MCP));//sets pin low
  analogWrite(IA_Proximal, 0);
  PORTB &= (~(1<<IB_Proximal));//sets pin low
  analogWrite(IA_Tension, 0);
  PORTA &= (~(1<<IB_Tension));//sets pin low
  
  tighten_pulleys(3300);
  
  TinyWireS.begin(I2C_SLAVE_ADDRESS);
  TinyWireS.onReceive(receiveEvent);
  TinyWireS.onRequest(requestEvent);

}

/*-------------------------------------------------------------------------------------------------------------------------------------------------*/

void loop()
{  
  if(PID_flag){
    setFingerPos(MCP_setPoint, proximal_setPoint);
  }else if(PID_cc_flag){
    co_contraction_PID(co_contraction);
  }else if(grip_flag){
    grip(800, 70, 70);
  }
//Might need to add this into the pidcc loop
  TinyWireS_stop_check();//Needs to be a tight loop apparently
}

/*-------------------------------------------------------------------------------------------------------------------------------------------------*/

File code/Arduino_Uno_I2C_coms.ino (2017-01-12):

/*--------------------------------------------------------------------------------------------------------------------
 * The code been developed for the Soft Touch Prosthetic Hand Project as part of the MEng Robotics ROCO504 Module at Plymouth University.
 * This code has been designed for the Arduino Uno microcontroller.
 * This file is subject to the terms and conditions defined in the file 'LICENSE.txt'.
 * Written by Isaac Chasteau
 --------------------------------------------------------------------------------------------------------------------*/

#include <Wire.h>

#define index_address 0x4
#define middle_address 0x5
#define ring_address 0x6
#define pinky_address 0x7
#define thumb_address 0x8

#define MCPOpen 20
#define proximalOpen 20

#define MCPClosed 70
#define proximalClosed 70

/*-------------------------------------------------------------------------------------------------------------------------------------------------*/

void demo(void){
int allDelay = 3500;
int singleDelay = 2000;

  sendAllFingersPosition(MCPOpen, proximalOpen, 'e');//open all
  sendPosition(MCPOpen, proximalOpen, 'e', 'e', thumb_address);//close thumb
  delay(allDelay*2);
//  sendAllFingersPosition(MCPClosed, proximalClosed, 'e');//close all
//  sendPosition(MCPClosed, proximalClosed, 'e', 'e', thumb_address);//close thumb
//  delay(allDelay);
//  sendAllFingersPosition(MCPOpen, proximalOpen, 'e');//open all
//  sendPosition(MCPOpen, proximalOpen, 'e', 'e', thumb_address);//close thumb
//  delay(allDelay);
  
  sendPosition(MCPClosed, proximalClosed, 0, 'e', pinky_address);//close pinky
  delay(singleDelay);
  sendPosition(MCPClosed, proximalClosed, 0, 'e', ring_address);//close ring
  delay(singleDelay);
  sendPosition(MCPClosed, proximalClosed, 0, 'e', middle_address);//close middle
  delay(singleDelay);
  sendPosition(MCPClosed, proximalClosed, 0, 'e', index_address);//close index
  delay(singleDelay);
  sendPosition(MCPClosed, proximalClosed, 'e', 'e', thumb_address);//close thumb
  delay(singleDelay);
  
  sendPosition(MCPOpen, proximalOpen, 0, 'e', pinky_address);//open pinky
  delay(singleDelay);
  sendPosition(MCPOpen, proximalOpen, 0, 'e', ring_address);//open ring
  delay(singleDelay);
  sendPosition(MCPOpen, proximalOpen, 0, 'e', middle_address);//open middle
  delay(singleDelay);
  sendPosition(MCPOpen, proximalOpen, 0, 'e', index_address);//open index
  delay(singleDelay);
  sendPosition(MCPOpen, proximalOpen, 'e', 'e', thumb_address);//open thumb
  delay(singleDelay);
  
  sendPosition(MCPOpen, proximalClosed, 0, 'e', pinky_address);//close pinky proximal
  delay(singleDelay);
  sendPosition(MCPOpen, proximalClosed, 0, 'e', ring_address);//close ring proximal
  delay(singleDelay);
  sendPosition(MCPOpen, proximalClosed, 0, 'e', middle_address);//close middle proximal
  delay(singleDelay);
  sendPosition(MCPOpen, proximalClosed, 0, 'e', index_address);//close index proximal
  delay(singleDelay);
  sendPosition(MCPOpen, proximalClosed, 'e', 'e', thumb_address);//close thumb proximal
  delay(singleDelay);
  
  sendAllFingersPosition(MCPClosed, proximalClosed, 'e');//close all
  sendPosition(MCPOpen, proximalOpen, 'e', 'e', thumb_address);//close thumb
  delay(allDelay);
  sendAllFingersPosition(MCPClosed, proximalOpen, 'e');//open all proximal
  sendPosition(MCPClosed, proximalOpen, 'e', 'e', thumb_address);//open thumb proximal
  delay(allDelay);
  sendAllFingersPosition(MCPOpen, proximalOpen, 'e');//open hand
  sendPosition(MCPOpen, proximalOpen, 'e', 'e', thumb_address);//open thumb
}

/*-------------------------------------------------------------------------------------------------------------------------------------------------*/

void sendAllFingersPosition(int MCP_pos, int proximal_pos, int co_contraction){
  char data[3];
  data[0] = MCP_pos;//MCP
  data[1] = proximal_pos;//Proximal
  data[2] = co_contraction;//Co-contraction
  data[3] = '\0';
  
  I2C_data(data, index_address);
  I2C_data(data, middle_address);
  I2C_data(data, ring_address);
  I2C_data(data, pinky_address);
}

/*-------------------------------------------------------------------------------------------------------------------------------------------------*/
//void test(void){
//  
//}
void sendPosition(int MCP_pos, int proximal_pos, int thumbServo_pos, int co_contraction, int address){
  char data[5];
  data[0] = MCP_pos;//MCP
  data[1] = proximal_pos;//Proximal
  data[2] = co_contraction;//Co-contraction
  if(address == thumb_address){
    data[3] = thumbServo_pos;
  }else{
    data[3] = '\0';
  }
  data[4] = '\0';
  
  I2C_data(data, address);
}

/*-------------------------------------------------------------------------------------------------------------------------------------------------*/

void I2C_data(char chars[], int slave_address){
  Wire.beginTransmission(slave_address); // transmit to device #8
  Wire.write(chars);// sends byte
  Wire.endTransmission();// stop transmitting
  delay(1); 
}

/*-------------------------------------------------------------------------------------------------------------------------------------------------*/
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

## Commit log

2017-01-12 folders
    individual folders
    [Certification_Keychain.step, Finger deflection data.xlsx, Hand 02.skp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]
2017-01-12 structured folders
    [Certification_Keychain.step, Finger deflection data.xlsx, Hand 02.skp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]
2017-01-12 more organisation
    [Certification_Keychain.step, Hand 02.skp, hand.skp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]
2017-01-13 more edits
    [Hand 02.skp, hand.skp]
